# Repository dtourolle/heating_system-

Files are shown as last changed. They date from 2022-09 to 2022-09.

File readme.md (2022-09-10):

# Heating control system

The 2nd law of thermodynamics states "that the total entropy of a system either increases or remains constant in any spontaneous process; it never decreases." Put in the context of heating a home the most you can hope for is the retain the heat through insulation (keeping the entropy between your house and the outside low), you will always loose the heat to the outside eventually.

This project was started during our first winter in the Netherlands. The radiators in our apartment were furnished with simple open/shut valves with little to no tuning possible, no thermostatic control. The increase in gas price during the pandemic caused my partner and I to experience a few shocks about the heating cost, this led me to think about how to tune the system to save us money.

The first step was solving an issue with the thermostat, this was a single Honeywell round thermostat with no clock for day/night timing and it was also mounted on probably the most poorly insulated wall of the house, so it would show a hybrid temperature of the outside and inside temperature. The thermostat uses OpenTherm to communicate with the boiler and also receive power (it's a 2 wire for power and data protocol). After considering the consequences of damaging the boiler electronics I decided to avoid interfacing with it directly, so the solution was to mechanically control the thermostat.

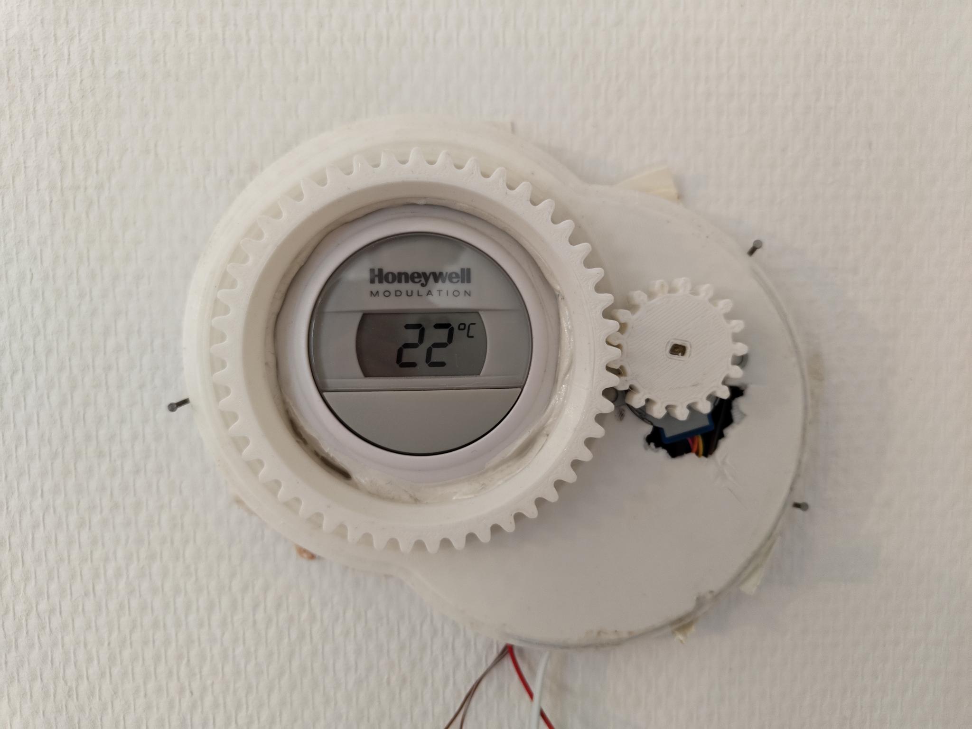
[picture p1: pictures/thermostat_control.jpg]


This involved printing a step down gear system from a 28byj stepper motor to the thermostat. The motor was controlled by an ESP32 connected to an MQTT server. This allowed an MQTT message to set the thermostat value through mechanical manipulation of the thermostat rather than electronic. Also of note is that the boiler is turned either on or off by the thermostat there is nothing in between for fine tuning of temperature.

The next step in the process was to control the follow into the radiators. There were two versions of this created. A first version used some mini-servo motors to rotate the valve and were attached directly to the radiator.



There were 2 of this version made but it suffered from a few design issues, firstly the servo motors were very loud, secondly connecting directly to the radiator allowed the PLA to warm up to a temperature where it become gummy and suffered from creep. Finally the use of ESP-01s made it hard to debug issues occurring on the device, and there was limited IOs to connected something to monitor or log.

The redesign of for version 2 learnt from these lessons and used the same 28byj stepper motor as used to control the thermostat. This motor has very little torque so it was coupled to a planetary gear box. To help debug issues an small oled binary display was added which printed information about the current state.

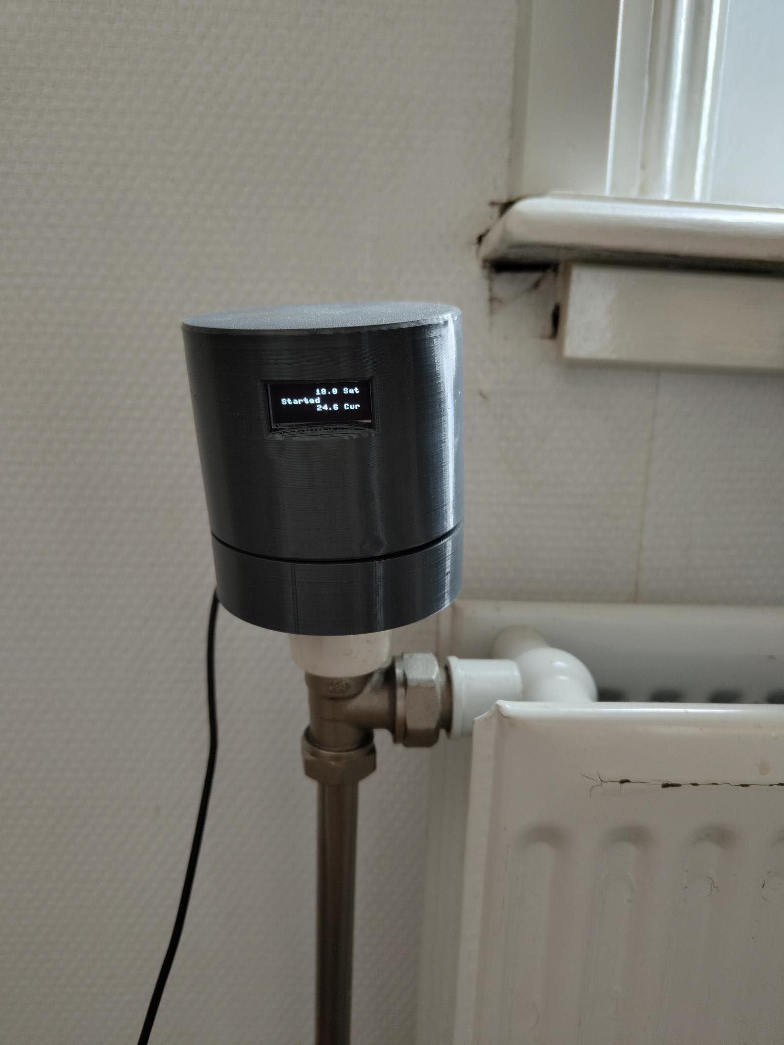
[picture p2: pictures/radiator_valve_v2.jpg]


So with these capable of actuating the system the next issues were sensing and controls.

Sensing was very straightforward, this was done with an ESP32 connected to an DHT22. The ESP32 was in deep sleep for a minute before reading the sensor and again logging the temperature via MQTT. There were a few different electronic designs for this, first using ESP-01s with [the deep sleep hack](https://www.instructables.com/Enable-DeepSleep-on-an-ESP8266-01/), but the possibility of reading with the ULP (the DHT22 has a 2 second warm up) then using the ESP32s main processor only for Wi-Fi based logging convinced me to switch boards. Sadly I never got the ULP aspect fully working. However the devices had ~2 months of battery and served their purpose well.

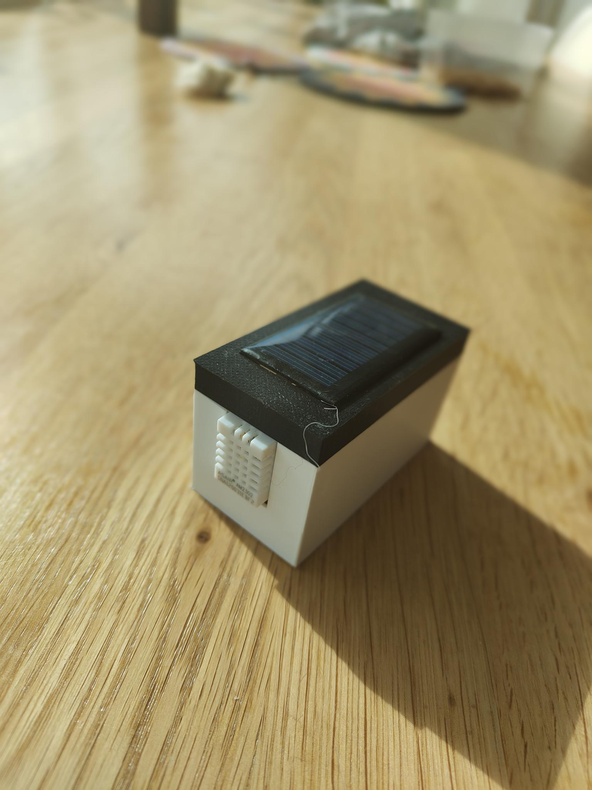
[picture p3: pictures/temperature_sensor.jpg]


The control system was very straightforward, if the temperature in a room was bellow a set point it register that the boiler was needed and also open the valve to the radiator. If the temperature was above a second set point it would close the valve and also register that the boiler wasn't needed. The server.py script allowed the number of rooms bellow their set points to be set before which the boiler would enable.

The set points were user determined either by an app or via an customized Lillygo 2020 watch. 

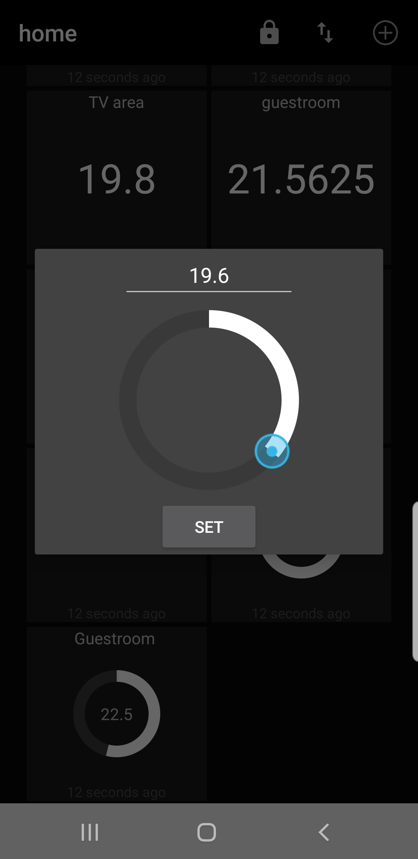
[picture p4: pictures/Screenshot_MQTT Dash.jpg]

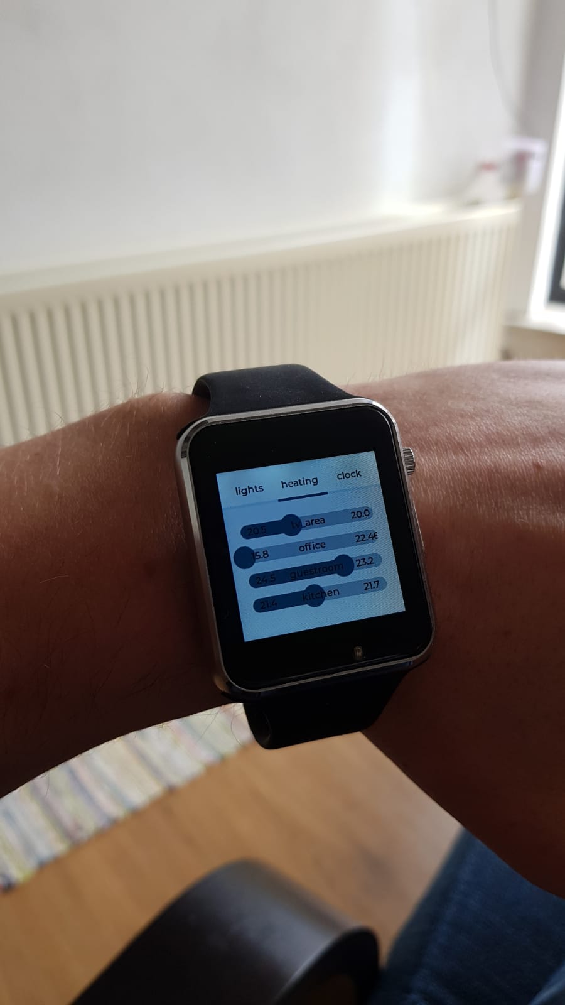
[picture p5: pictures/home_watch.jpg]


This all comes together in the following system, where the connections between the elements are shown.

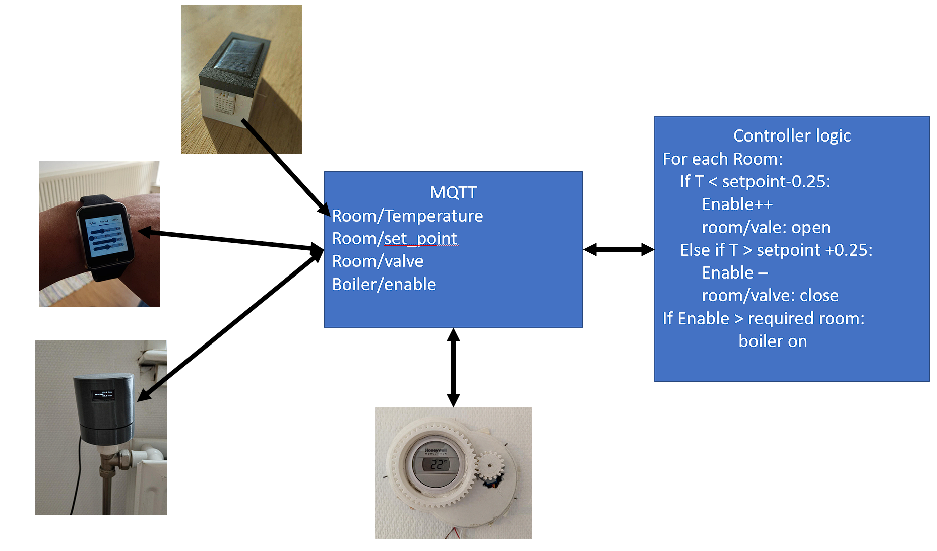
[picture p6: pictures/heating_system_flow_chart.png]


The thermometer has a unidirectional connection to the system, it simply sends the temperature (and humidity) to the MQTT server on an roughly 1 minute basis. The MQTT server is also connected to by the [radiator_server.py](src/server/radiator_server.py) script, which stores the values in a database (very useful for tuning the system) and also orchestrates the opening and closing of the valves and the activation of the boiler, again by posting to an MQTT server. The valves and thermostat listen to this MQTT server and behave accordingly, the thermostat also uses the MQTT server to store it's state, so should it reboot it will reload the currently set value. The valves connect to show the set points and current temperature. Finally the user can set the settings with either the watch or the android application.

A recording for a single room will look like this:

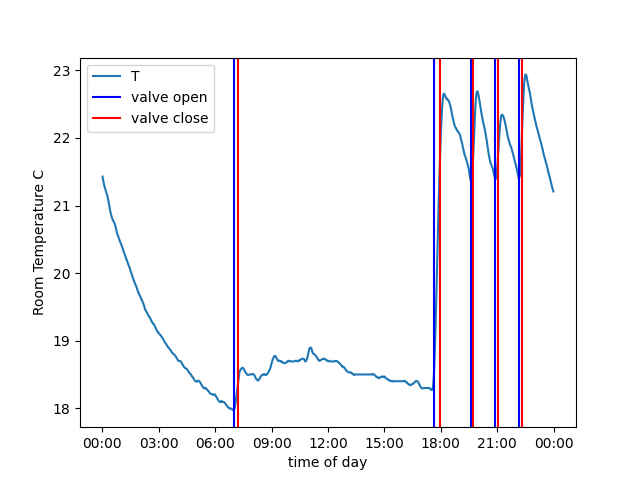
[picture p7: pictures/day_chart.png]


In the morning the system turns one at 7am and heats the room to the set point of about 18.5 degrees. This room likely wasn't used that day until about 18:00 when the set point was evidently changed to about 21 degrees. The system can be seen opening and closing the valve, while the temperature overshoots by about 1.5 degree each cycle.

The same plot can be made for all rooms simultaneously.
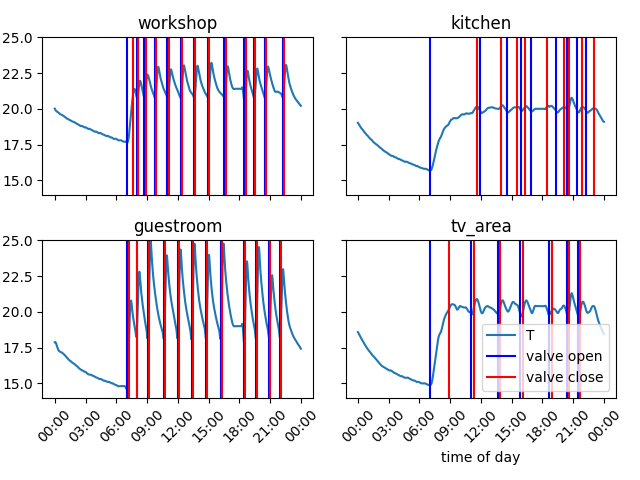
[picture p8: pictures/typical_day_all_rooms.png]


This is a recording of a typical day and the differences in the valve behaviour for the different rooms underlines the initial issue with the heating system. As the valves were not thermostatic some of the rooms would have been saunas with the heating make the coldest room comfortable, or the coldest room would have likely been bellow 16 degrees with the warmest at 21.

The other big advantage of the system was the ability to just turn down rooms that were not in use. This is an image from a weekend where lots of time was spend in the kitchen and watching TV.

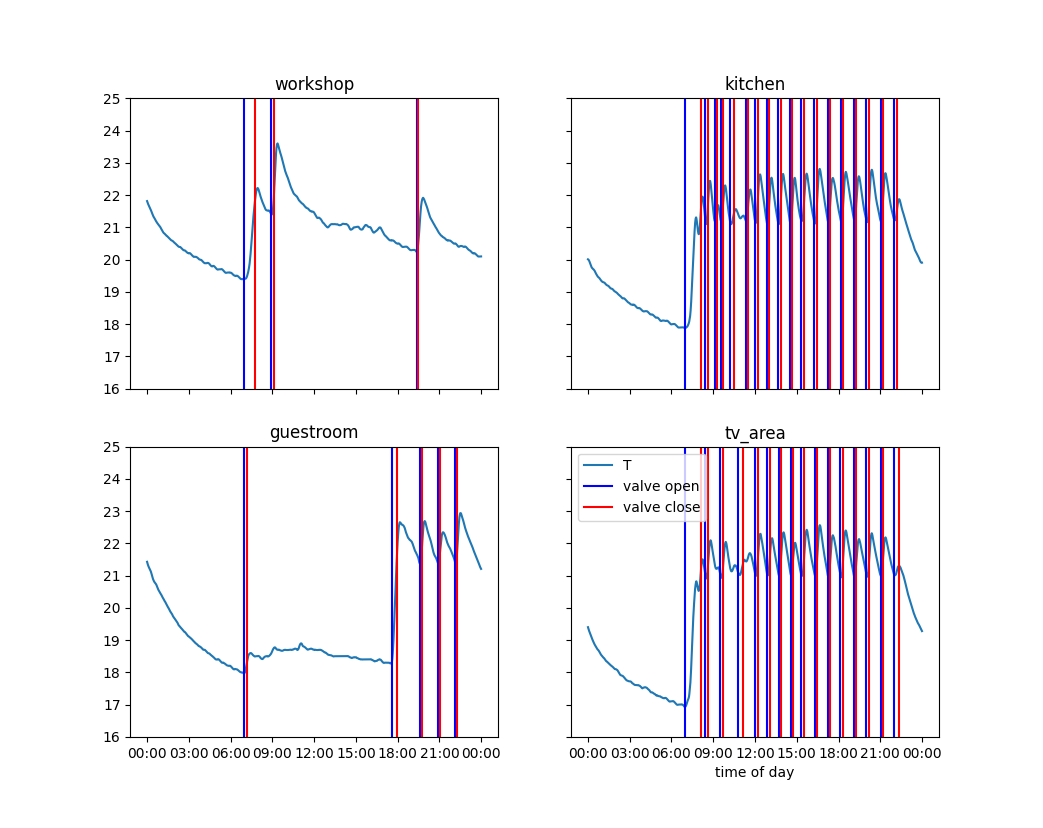
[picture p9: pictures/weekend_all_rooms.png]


The guestroom and workshop have been turned down during the day and remain cool, or at least unheated. While the kitchen and tv area are warmed. 

## How to use this

### building the devices
The devices are all 3d printed, the stl files can be found [here](stl), while for the devices designed in FreeCAD the drawings are [here](CAD), I am more than wiling to convert the missing drawings to FreeCAD if there is a request. All of the electronics rely on WEMOS ESP32 board, and 28byj stepper motor with drivers.

#### Radiator Valve
For the valve controller the following assembly is required.

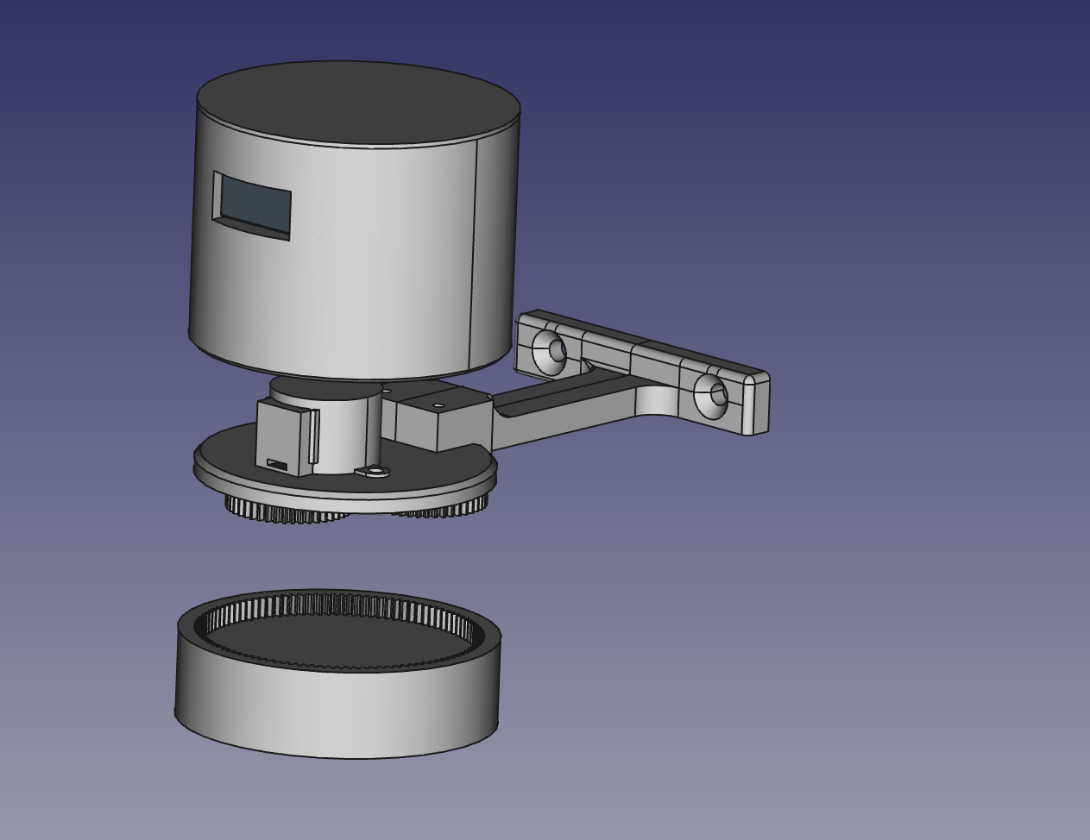
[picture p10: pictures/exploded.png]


The motor and [wall bracket](stl/radiator_valve/bracket.stl) should be mounted on the [carrier base](stl/radiator_valve/carrier_base.stl) using m3 screw. The bracket might need to be pre-tapped depending on the printer settings. The ESP32 and stepper driver can be mated at the GPIO see [here](src/valves/main.py) for port numbers. For the [OLD display](https://www.waveshare.com/0.91inch-oled-module.htm) depending on the version used you will need to solder wires on with about 8cm in length. I used the cheapest version from amazon and they worked fine. This also needs to be wired to the ESP32 for GPIO see [here](src/valves/main.py).  THe screen can then be secured in place within the [upper case](stl/radiator_valve/case.stl) with scotch tape and/or glue. The ESP32 can be power via USB and the VCC of the board should be connected to the stepper motor.
The planetary gear box should slot together, if it is a little tight then twisting it during assembly will help get it together. Using the ESP32 test the rotation of the gear box and the torque, a tight gear box might need some lubrication, also when applying a resistance check if the gears try to eject themselves from the gear box, if this happens it might be worth flipping some of the [planet gears](stl/radiator_valve/planet_gear.stl), as the 3d printing process might have left them tapered which causes them to push out of the [ring gear](stl/radiator_valve/connector.stl).

The whole lower assembly can be mounted on the radiator valve, mark the holes on the wall for the [wall bracket](stl/radiator_valve/bracket.stl) for drilling and attaching with rawlplugs and screws. Once the lower assembly is attached the [upper case](stl/radiator_valve/case.stl) assembly can be seated in place. If needed some soft putty of scotch can be used to secure it in place.

It is worth taking time to measure the distance between the wall and the radiator valve, the adjust the [wall bracket](stl/radiator_valve/bracket.stl) either by stretching the mesh or using the [free cad file](CAD/radiator_valve/connector.FCStd).

#### Thermostat control

The thermostat control was electronically very similar to the radiator valve, this consisted of a ESP32, in this case it was a raw module, that was all I had available and I would recommend a WEMOS ESP32 or other such dev board, the software can be found [here](src/thermostat/).

The assembly consisted of [a case](/stl/thermostat_controller/case_5.stl) containing the electronics and the motor. While gears were attached to the [motor](/stl/thermostat_controller/gear_1.stl) and the [thermostat](/stl/thermostat_controller/wheel_1.stl). The thermostat gear was secured using white re-usable adhesive putty, while the drive gear was press fitted.

#### Thermometers

These used a DF Robot ESP32 Firebeetle board, connected to an DHT22, a 18650 battery, and a 30ma Solar panel. Unfortunaly I have not been able to track down the STL files and the original CAD files were made using an educational licensed Siemens NX. I am more than happy to re-create them in FreeCAD on demand.

#### Flashing the devices
All of the devices run micropython, if the latest version does not work these were flashed with versions from spring 2021. Once the devices have micropython copy the source code across and make sure you convert the "example_settings.py" to a "settings.py".

### Setting up the server

This project runs on a Raspberry Pi, it is very light weight. There are some software requirements that your package manager can solve:

- [mosquitto](https://mosquitto.org/) (or another MQTT broker)
- Python >3.5
- mariaDB

Once these are setup all you need to do make a "config.py" out of the [example_config.py](/src/server/example_config.py) and run the [main script](src/server/radiator_server.py). Ideally this should be configured as a systemd module or a chronjob.

There will likely be teething issues, either from this software or from things overlook during the setup. Most likely the firewall will be blocking MQTT and mariaDB when this first starts, check for your linux distro how to open the ports. Another issue which might occur is if you do not provide the raspberry pi with a static IP address, if during reboot it looses it's address this will be a huge pain, so ensure it is indeed static to start with. Finally when the MQTT server restarts it is advised to restart all the devices manually with a power cycle, they are configured to reconnect on failure but this is the safest option.

[historic Dutch data](https://daggegevens.knmi.nl/klimatologie/uurgegevens)

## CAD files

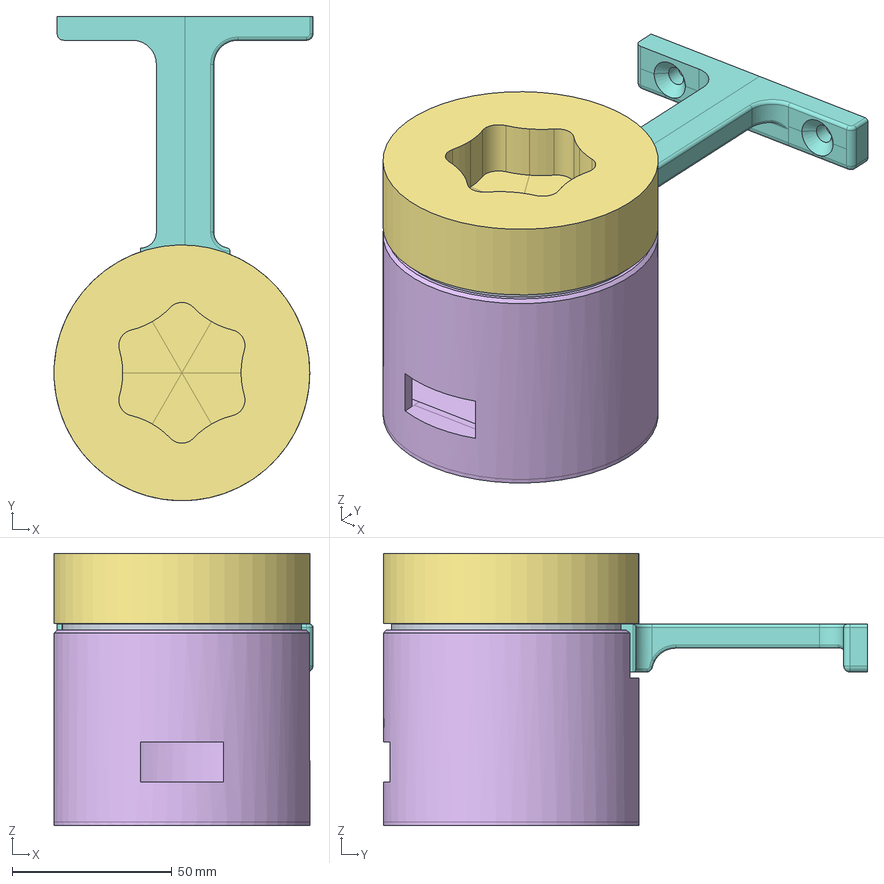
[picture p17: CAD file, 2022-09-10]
CAD/radiator_valve/assembly.FCStd
81.0 x 151.5 x 85.1 mm
carrier_case_001
sun_gear_001
planet_gear_001
planet_gear_002
planet_gear_003
case_001
ring_connector_001
connector_001

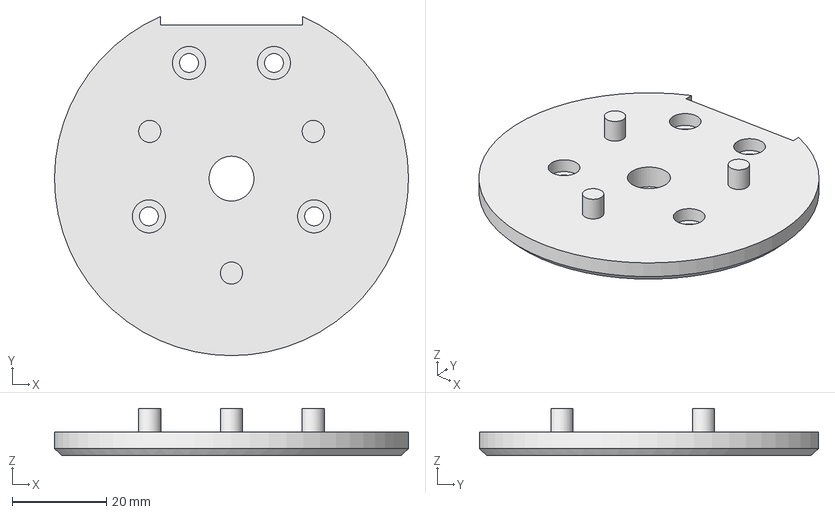
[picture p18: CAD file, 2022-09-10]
CAD/radiator_valve/carrier_case.FCStd
75.0 x 71.9 x 10.0 mm

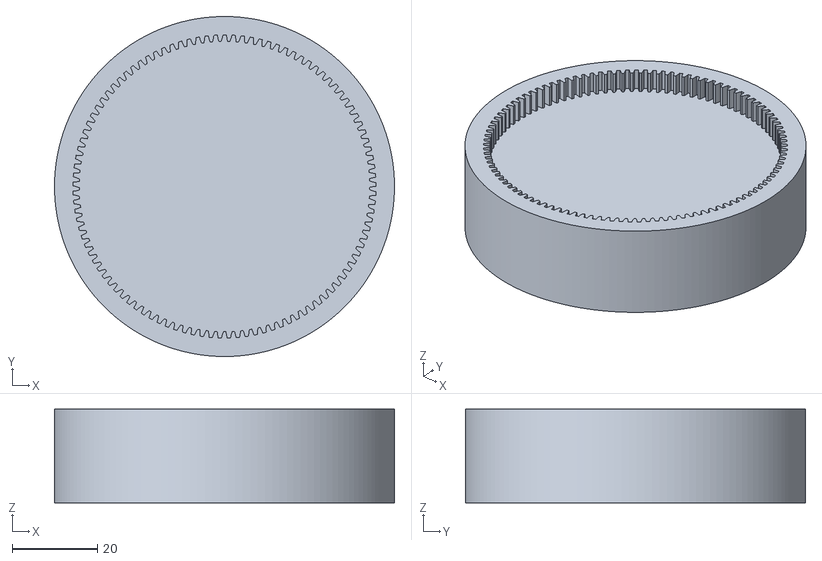
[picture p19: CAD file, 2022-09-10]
stl/radiator_valve/connector_bk.stl
80.0 x 80.0 x 22.0

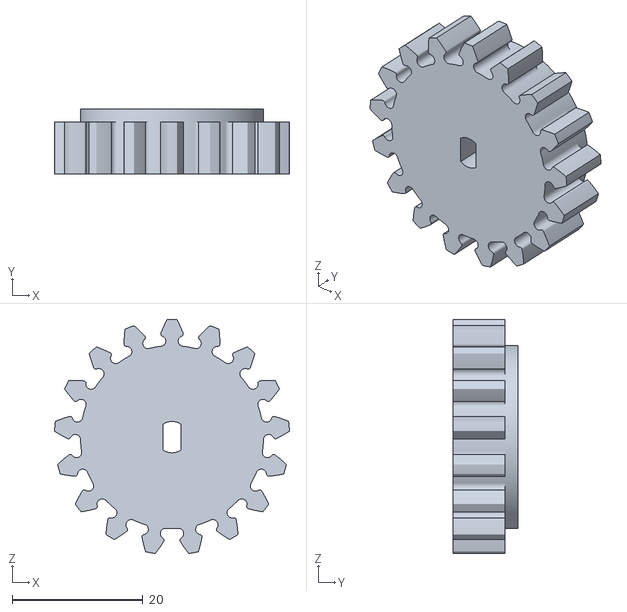
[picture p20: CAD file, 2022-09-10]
stl/thermostat_controller/gear_1.stl
36.0 x 10.0 x 35.8

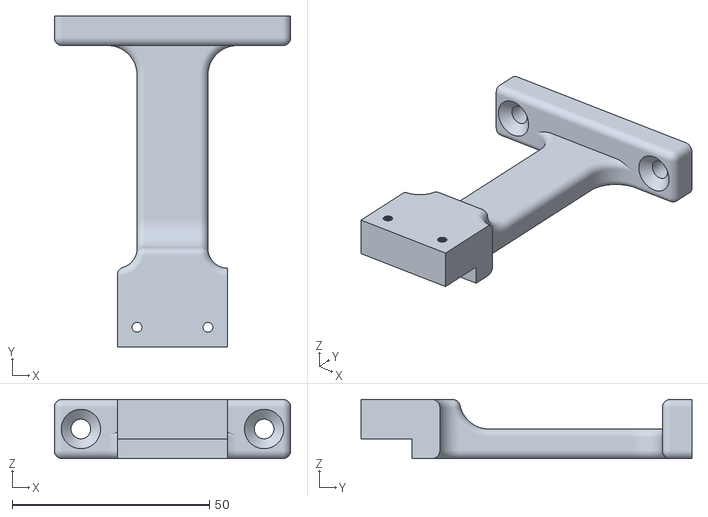
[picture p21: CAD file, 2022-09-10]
stl/radiator_valve/bracket_bk.stl
60.0 x 84.0 x 15.0

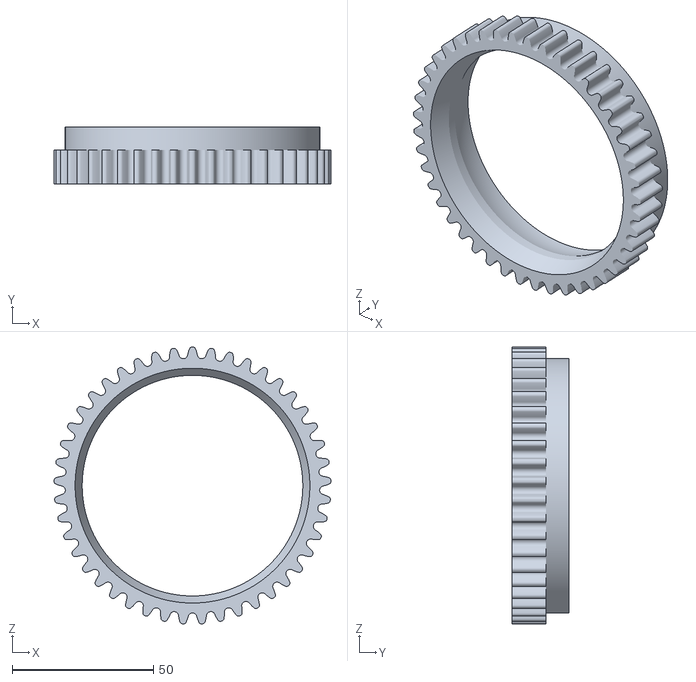
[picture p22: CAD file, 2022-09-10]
stl/thermostat_controller/wheel_1.stl
98.0 x 20.0 x 97.9

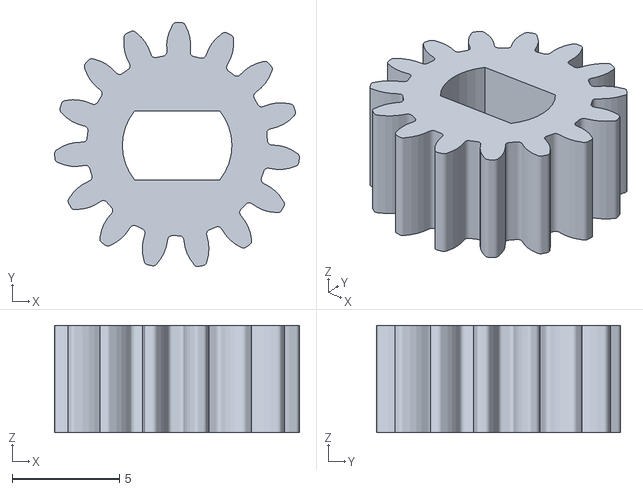
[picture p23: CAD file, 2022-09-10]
stl/radiator_valve/sun_gear_bk.stl
11.4 x 11.4 x 5.00

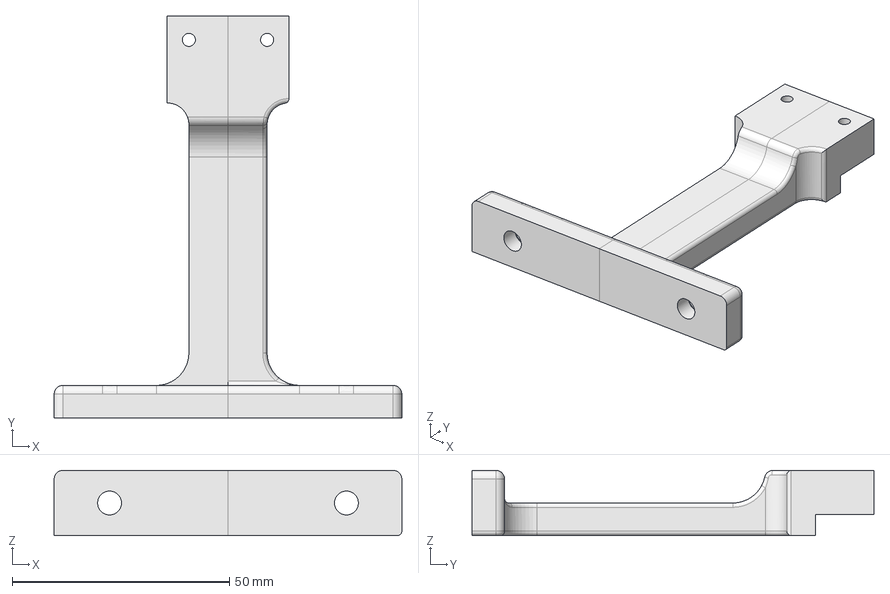
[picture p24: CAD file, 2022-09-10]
CAD/radiator_valve/connector.FCStd
80.0 x 92.5 x 15.0 mm

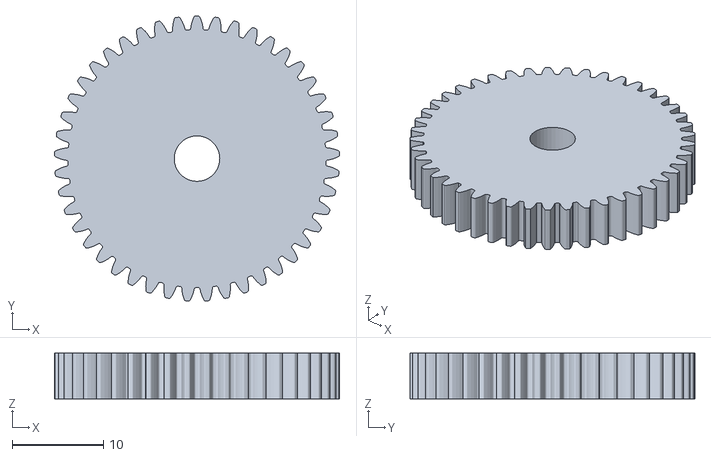
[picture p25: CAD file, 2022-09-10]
stl/radiator_valve/planet_gear_bk.stl
31.3 x 31.3 x 5.00

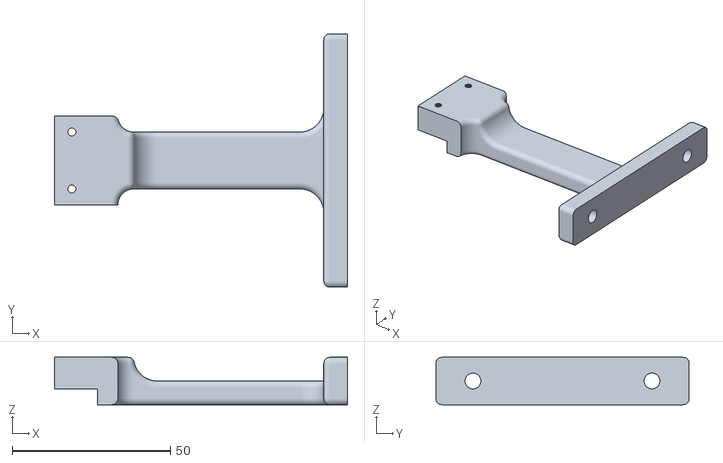
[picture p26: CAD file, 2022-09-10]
stl/radiator_valve/bracket.stl
92.5 x 80.0 x 15.0

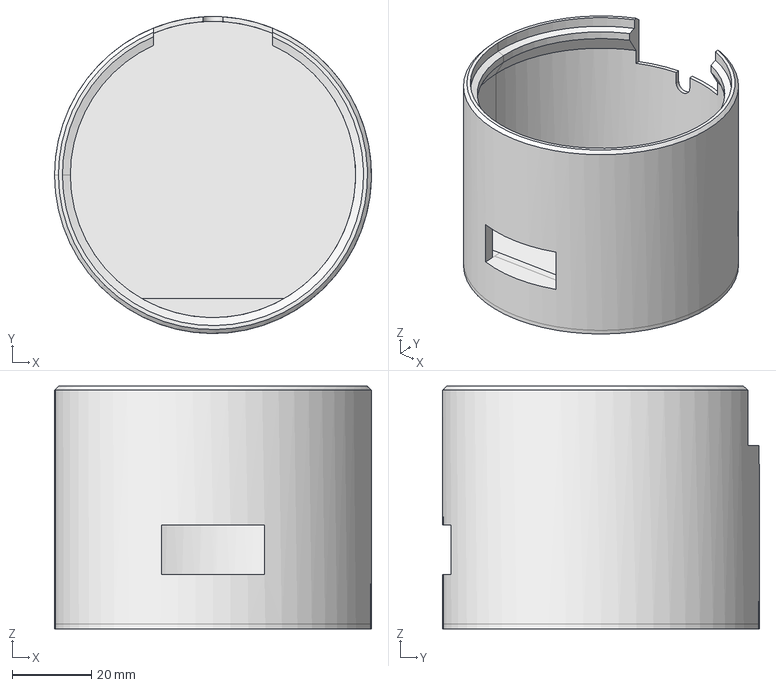
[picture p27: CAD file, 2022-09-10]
CAD/radiator_valve/case.FCStd
80.0 x 80.0 x 61.2 mm

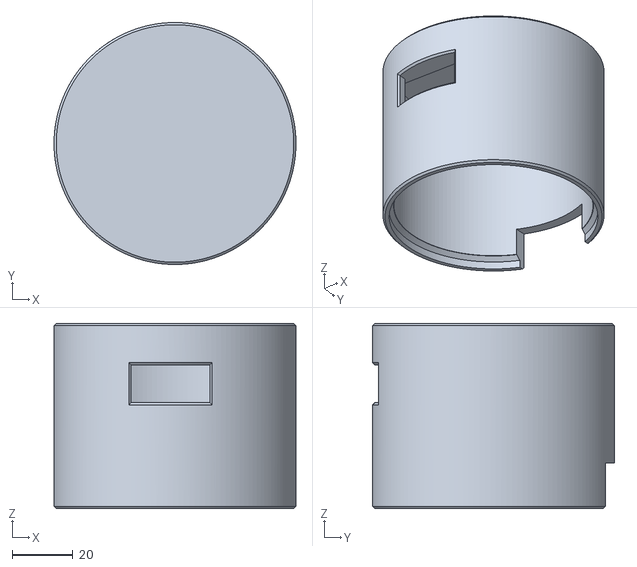
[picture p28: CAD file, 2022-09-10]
stl/radiator_valve/case_bk.stl
80.0 x 80.0 x 61.2

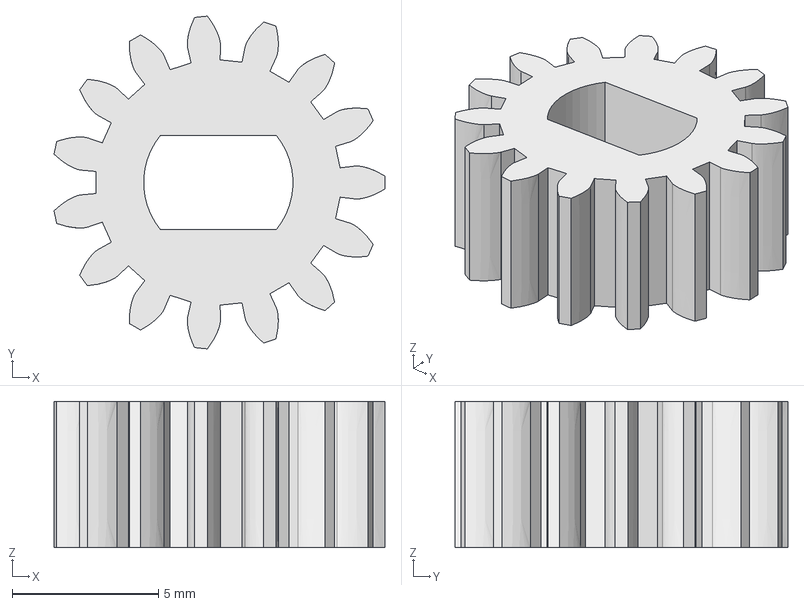
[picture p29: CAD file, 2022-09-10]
CAD/radiator_valve/sun_gear.FCStd
11.3 x 11.4 x 5.00 mm

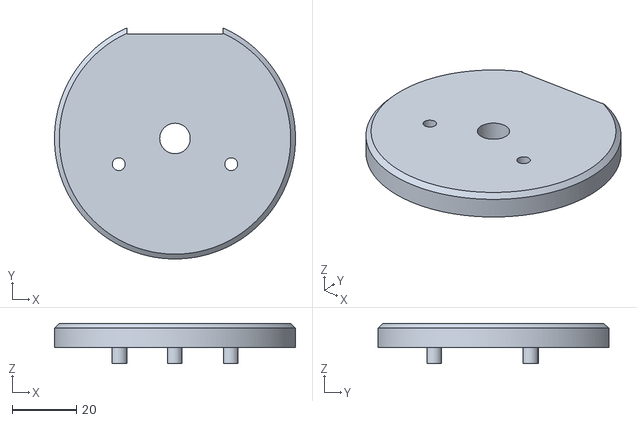
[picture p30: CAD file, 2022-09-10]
stl/radiator_valve/carrier_base_bk.stl
75.0 x 71.9 x 12.5

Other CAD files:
CAD/radiator_valve/ring_connector.FCStd
CAD/radiator_valve/planet_gear.FCStd
stl/radiator_valve/carrier_base.stl
stl/radiator_valve/ring_geat.stl
stl/radiator_valve/case.stl
stl/radiator_valve/connector.stl
stl/radiator_valve/planet_gear.stl
stl/radiator_valve/sun_gear.stl

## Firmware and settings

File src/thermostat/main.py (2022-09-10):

try:
    import usocket as socket
except:
    import socket
import ustruct as struct
from ubinascii import hexlify
import esp
import machine
import network


from time import sleep
import socket
import time

try:
    import binascii
except ImportError:
    import ubinascii as binascii
import utime 

from settings import *
from uln2003 import Stepper, FULL_STEP
            
class thermostat:

    def __init__(self,level=17.5):
        self.level = level
        self.motor = Stepper(FULL_STEP,27,33,23,32,delay=5000)
        self.steps_per_degree = 500/(17.75-9)
        self.on_level = 21.5
        self.off_level = 15
    def set_temperature(self,T):
        diff = T -self.level
        steps = abs(self.steps_per_degree*diff)
        if diff<0:
            self.motor.step(steps,1)
        if diff>=0:
            self.motor.step(steps,-1)
        self.level = T

    def on(self):
        self.set_temperature(self.on_level)

    def off(self):
        self.set_temperature(self.off_level)

    def neutral(self):
        self.set_temperature(17.5)

class MQTT(object):
    s = None
    addr = None
    

    def __init__(self, host, port=1883,device_name="Thermostat"):
        self.addr = socket.getaddrinfo(host, port)[0][4]
        self.reset_socket()
        self.device_name = device_name
        self.pid=0
    def reset_socket(self):
        self.s = socket.socket()

    def connect(self):
        address = self.addr
        self.s.connect(address)
        self.s.send(self.mtpConnect(self.device_name))

    def disconnect(self):
        self.s.send(self.mtpDisconnect())
        self.s.close()

    def publish(self, topic, data, sleep=1):
        self.s.send(self.mtpPub(topic, bytes(str(data), 'ascii')))
        if sleep:
            time.sleep(sleep)

    def recv(self, length=4096):
        return binascii.hexlify(self.s.recv(length))

    @staticmethod
    def mtStr(s):
        return bytes([len(s) >> 8, len(s) & 255]) + s.encode('utf-8')

    @staticmethod
    def mtPacket(cmd, variable, payload):
        return bytes([cmd, len(variable) + len(payload)]) + variable + payload

    def mtpConnect(self, name):
        return self.mtPacket(
            0b00010000,
            self.mtStr("MQTT") +  # protocol name
            b'\x04' +  # protocol level
            b'\x00' +  # connect flag
            b'\xFF\xFF',  # keepalive
            self.mtStr(name)
        )

    @staticmethod
    def mtpDisconnect():
        return bytes([0b11100000, 0b00000000])

    def mtpPub(self, topic, data):
        return self.mtPacket(0b00110001, self.mtStr(topic), data)

    def subscribe(self, topic, qos=0):
        assert self.cb is not None, "Subscribe callback is not set"
        pkt = bytearray(b"\x82\0\0\0")
        self.pid += 1
        struct.pack_into("!BH", pkt, 1, 2 + 2 + len(topic) + 1, self.pid)
        #print(hex(len(pkt)), hexlify(pkt, ":"))
        self.s.write(pkt)
        self._send_str(topic)
        self.s.write(qos.to_bytes(1, "little"))
        while 1:
            op = self.wait_msg()
            if op == 0x90:
                resp = self.s.read(4)
                #print(resp)
                assert resp[1] == pkt[2] and resp[2] == pkt[3]
                if resp[3] == 0x80:
                    pass
                return

    def _send_str(self, s):
        self.s.write(struct.pack("!H", len(s)))
        self.s.write(s)

    def _recv_len(self):
        n = 0
        sh = 0
        while 1:
            b = self.s.read(1)[0]
            n |= (b & 0x7f) << sh
            if not b & 0x80:
                return n
            sh += 7

    def set_callback(self, f):
        self.cb = f
    # Wait for a single incoming MQTT message and process it.
    # Subscribed messages are delivered to a callback previously
    # set by .set_callback() method. Other (internal) MQTT
    # messages processed internally.
    def wait_msg(self):
        res = self.s.read(1)
        self.s.setblocking(True)
        if res is None:
            return None
        if res == b"":
            raise OSError(-1)
        if res == b"\xd0":  # PINGRESP
            sz = self.s.read(1)[0]
            assert sz == 0
            return None
        op = res[0]
        if op & 0xf0 != 0x30:
            return op
        sz = self._recv_len()
        topic_len = self.s.read(2)
        topic_len = (topic_len[0] << 8) | topic_len[1]
        topic = self.s.read(topic_len)
        sz -= topic_len + 2
        if op & 6:
            pid = self.s.read(2)
            pid = pid[0] << 8 | pid[1]
            sz -= 2
        msg = self.s.read(sz)
        self.cb(topic, msg)
        if op & 6 == 2:
            pkt = bytearray(b"\x40\x02\0\0")
            struct.pack_into("!H", pkt, 2, pid)
            self.s.write(pkt)
        elif op & 6 == 4:
            assert 0

    # Checks whether a pending message from server is available.
    # If not, returns immediately with None. Otherwise, does
    # the same processing as wait_msg.
    def check_msg(self):
        self.s.setblocking(False)
        return self.wait_msg()

thremo = thermostat()


def sub_cb(topic, msg):
    if topic == b"boiler/set":
        if msg == b"on":
            print("open")
            thremo.on()
            

        elif msg == b"off":
            print("close")
            thremo.off()
        else:
            try:
                val = float(msg)
                thremo.set_temperature(val)
            except:
                print("invalid temperature")
        print(str(thremo.level))
        conn.publish('boiler/value',str(thremo.level))
    elif topic == b"boiler/value":
        try:
            print("starting: level",float(msg))
            thremo.level = float(msg)
        except:
            print("serious error")
    


def start_cb(topic,msg):

    try:
        print("starting: level",float(msg))
        thremo.level = float(msg)
    except:
        print("serious error")


print("start wifi radio")
station = network.WLAN(network.STA_IF)

station.active(True)
station.connect(wifi_ssid, wifi_passwd)
attempts = 0

while station.isconnected() == False:
  sleep(0.1)
  attempts +=1
  if attempts>100:

        time.sleep(30)
        attempts=0

ap_if = network.WLAN(network.AP_IF)
ap_if.active(False)
print("wifi connected")
conn = MQTT(server)
conn.set_callback(start_cb)
conn.connect()
conn.subscribe("boiler/value")
conn.check_msg()
conn.disconnect()
time.sleep(1)
conn = MQTT(server)
conn.set_callback(sub_cb)
conn.connect()
conn.subscribe("boiler/set")
#conn.publish('light/stairs/set','toggle')
try:
    while True:
        conn.check_msg()
        if station.isconnected() == False:
            station = network.WLAN(network.STA_IF)
            station.active(True)
            station.connect(wifi_ssid, wifi_passwd)
            attempts = 0

            while station.isconnected() == False:

                time.sleep(0.1)

                attempts +=1

                if attempts>100:
                        time.sleep(30)
        sleep(5)
except:
    machine.reset()



#loop.create_task(encoder_loop(enc))
#try:

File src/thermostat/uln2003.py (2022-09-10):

import machine

# (c) IDWizard 2017
# MIT License.
import time

LOW = 0
HIGH = 1
FULL_ROTATION = int(4075.7728395061727 / 8) # http://www.jangeox.be/2013/10/stepper-motor-28byj-48_25.html

HALF_STEP = [
    [HIGH, LOW, LOW, LOW],
    [HIGH, HIGH, LOW, LOW],
    [LOW, HIGH, LOW, LOW],
    [LOW, HIGH, HIGH, LOW],
    [LOW, LOW, HIGH, LOW],
    [LOW, LOW, HIGH, HIGH],
    [LOW, LOW, LOW, HIGH],
    [HIGH, LOW, LOW, HIGH],
]

FULL_STEP = [
 [HIGH, HIGH, LOW, LOW],
 [LOW, HIGH, HIGH, LOW],
 [LOW, LOW, HIGH, HIGH],
 [HIGH, LOW, LOW, HIGH]
]

class Command():
    """Tell a stepper to move X many steps in direction"""
    def __init__(self, stepper, steps, direction=1):
        self.stepper = stepper
        self.steps = steps
        self.direction = direction

class Driver():
    """Drive a set of motors, each with their own commands"""

    @staticmethod
    def run(commands):
        """Takes a list of commands and interleaves their step calls"""
        
        # Work out total steps to take
        max_steps = sum([c.steps for c in commands])

        count = 0
        while count != max_steps:
            for command in commands:
                # we want to interleave the commands
                if command.steps > 0:
                    command.stepper.step(1, command.direction)
                    command.steps -= 1
                    count += 1
        
class Stepper():
    def __init__(self, mode, pin1, pin2, pin3, pin4, delay=7500):
        self.mode = mode
        self.pin1 = machine.Pin(pin1, machine.Pin.OUT)
        self.pin2 = machine.Pin(pin2, machine.Pin.OUT)
        self.pin3 = machine.Pin(pin3, machine.Pin.OUT)
        self.pin4 = machine.Pin(pin4, machine.Pin.OUT)
        self.delay = delay  # Recommend 10+ for FULL_STEP, 1 is OK for HALF_STEP
        
        # Initialize all to 0
        self.reset()
        
    def step(self, count, direction=1):
        """Rotate count steps. direction = -1 means backwards"""
        for x in range(count):
            for bit in self.mode[::direction]:
                self.pin1.value(bit[0]) 
                self.pin2.value(bit[1]) 
                self.pin3.value(bit[2]) 
                self.pin4.value(bit[3]) 
                time.sleep_us(self.delay)

        self.reset()
        
    def reset(self):
        # Reset to 0, no holding, these are geared, you can't move them
        self.pin1.value(0) 
        self.pin2.value(0) 
        self.pin3.value(0) 
        self.pin4.value(0) 

if __name__ == '__main__':
    pass
    #s1 = Stepper(HALF_STEP, microbit.pin16, microbit.pin15, microbit.pin14, microbit.pin13, delay=5)    
    #s2 = Stepper(HALF_STEP, microbit.pin6, microbit.pin5, microbit.pin4, microbit.pin3, delay=5)   
    #s1.step(FULL_ROTATION)
    #s2.step(FULL_ROTATION)

    #runner = Driver()
    #runner.run([Command(s1, FULL_ROTATION, 1), Command(s2, FULL_ROTATION/2, -1)])
